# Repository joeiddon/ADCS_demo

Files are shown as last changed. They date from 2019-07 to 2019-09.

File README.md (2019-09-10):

ADCS Demo
=========

#### An Attitude Determination and Control System (ADCS) demo.

Created for [Open Cosmos](https://www.open-cosmos.com/), this project uses off-the-shelf components to demonstrate the principle of operation of an ADCS.

See videos and pictures of the development process and a working protoype in [this Google Photos Album](https://photos.app.goo.gl/isr3sSZi2DETxmJA6).

---

### What is an ADCS?

This system is an essential component of most spacecraft. It is the general term for the hardware and software which keeps a satellite orientated in space.

Although the objective of an ADCS is common amongst all systems, the way this is achieved varies. The many different variations and their characteristics are summarised in [this NASA paper](https://ntrs.nasa.gov/archive/nasa/casi.ntrs.nasa.gov/20110007876.pdf).

### Reaction wheel as the actuator

A wide variey of actuator types can be used in an ADCS. For example: magnetic torquers, thrusters and reaction wheels. This demo uses a reaction wheel.

A reaction wheel works by spinning a wheel up to a high angular velocity, then applying a torque to change this velocity. Due to Newton's Third Law, the body must experience an equal and opposite torque to the wheel - accelerating it in the opposite direction. Alternatively, this could be thought of in terms of the [law of conservation of angular momentum](http://www.feynmanlectures.caltech.edu/I_18.html) if we assume no external torque on the system as a whole.

Through a PID feedback loop, this mechanism can precisely control the orientation of a spacecraft.

The sensor used as an input to this PID loop varies for real applications (e.g. Sun sensor, Earth sensor, Star Tracker, Magnetometer etc.). This demo was designed to track the position of a torch, so two light sensors are used; their difference in readings providing an error value to work with.

### Demo hardware specifics

Three reaction wheels would be required to orient in all three axis. For simplicity of design, this demo focusses on controlling the attitude in a singular axis. In order to do this, the demo is freely suspended by a piece of thread which isolates the vertical axis.

The demonstration consists of the following components:

Part | Component Type Used
--- | ---
Processor | Arduino Nano
Motor | Brushless DC from Hard Drive
Frame | 3D Printed; Designed in OpenScad
Power | Two 1S Lipos in Series (7.4V)
Light Sensors | LDRs

### Prototype

To verify that the above set of components would be appropriate, a prototype was built first ([video](https://photos.app.goo.gl/x1hWNtvbokYaZJKe7)). This used a breadboard to host the MOSFET power distribution, and a bench power supply instead of lipo batteries. It suceeded in proving that, amongst other things, the motor would be adequate.

### Pictures

Below are some pictures of the design process. For more images, see the `images` directory.

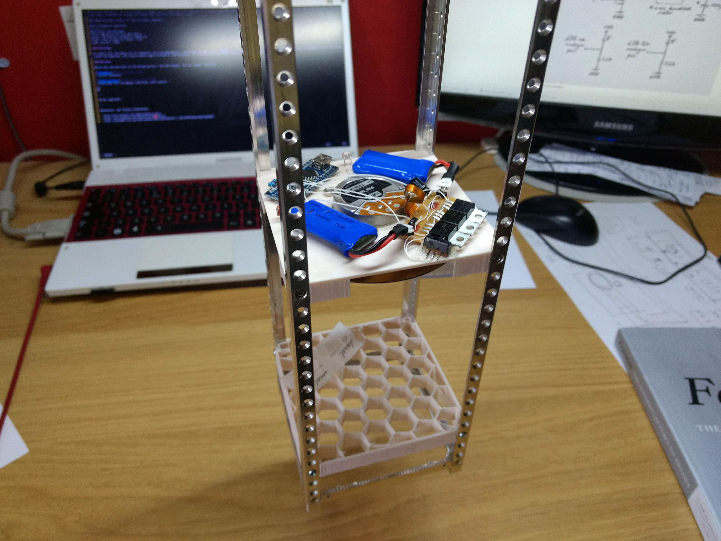
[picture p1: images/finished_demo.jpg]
Finished Demo

*Finished Demo*

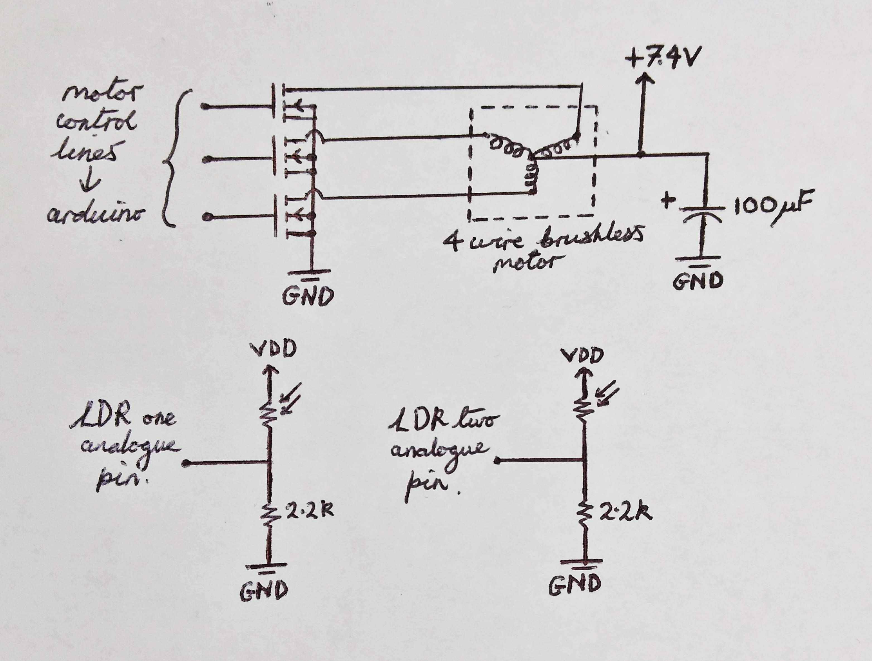
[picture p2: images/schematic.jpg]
Schematic

*Circuit schematic* ([better diagram](https://xkcd.com/730/))

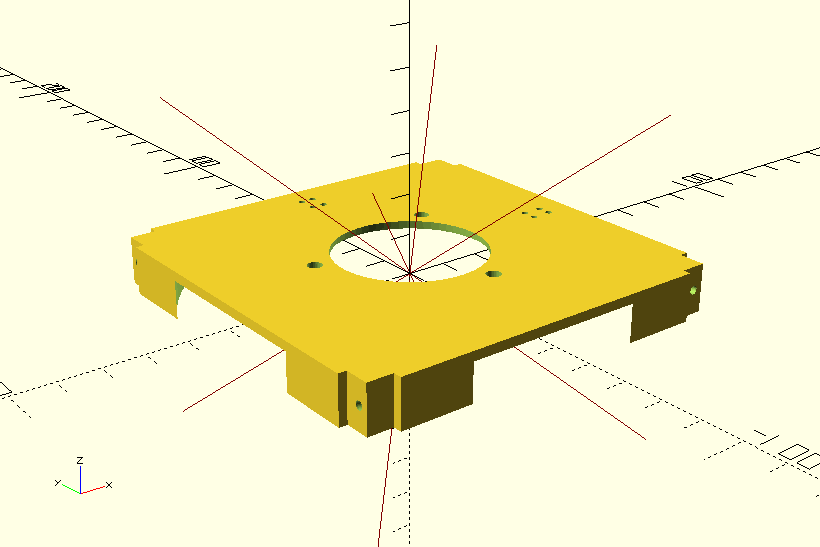
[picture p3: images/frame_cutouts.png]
Frame Cutouts

*Frame that fits the BeeKit interface; with cutouts.*

---

#### References, and further information:

- http://www.ece3sat.com/cubesatmodules/adcs/
- https://en.wikipedia.org/wiki/Attitude_control
- http://citeseerx.ist.psu.edu/viewdoc/download?doi=10.1.1.823.8473&rep=rep1&type=pdf

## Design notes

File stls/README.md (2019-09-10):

This folder contains the `.stl` 3D model files that are ready to be sent to a 3D printer to be sliced and printed.

For descriptions of the designs, see the README in the sibling `/scads` directory.

To view any particular design just click on it and GitHub will render it here in the browser for you.

You can then right click on the `Raw` button and select "Save link as..." to download it if you do not want to clone this whole repository.

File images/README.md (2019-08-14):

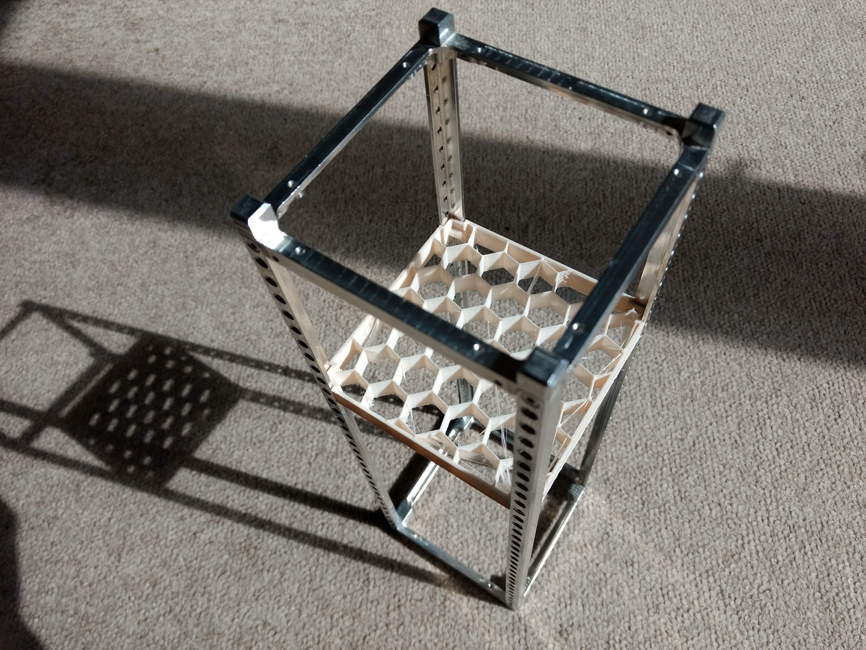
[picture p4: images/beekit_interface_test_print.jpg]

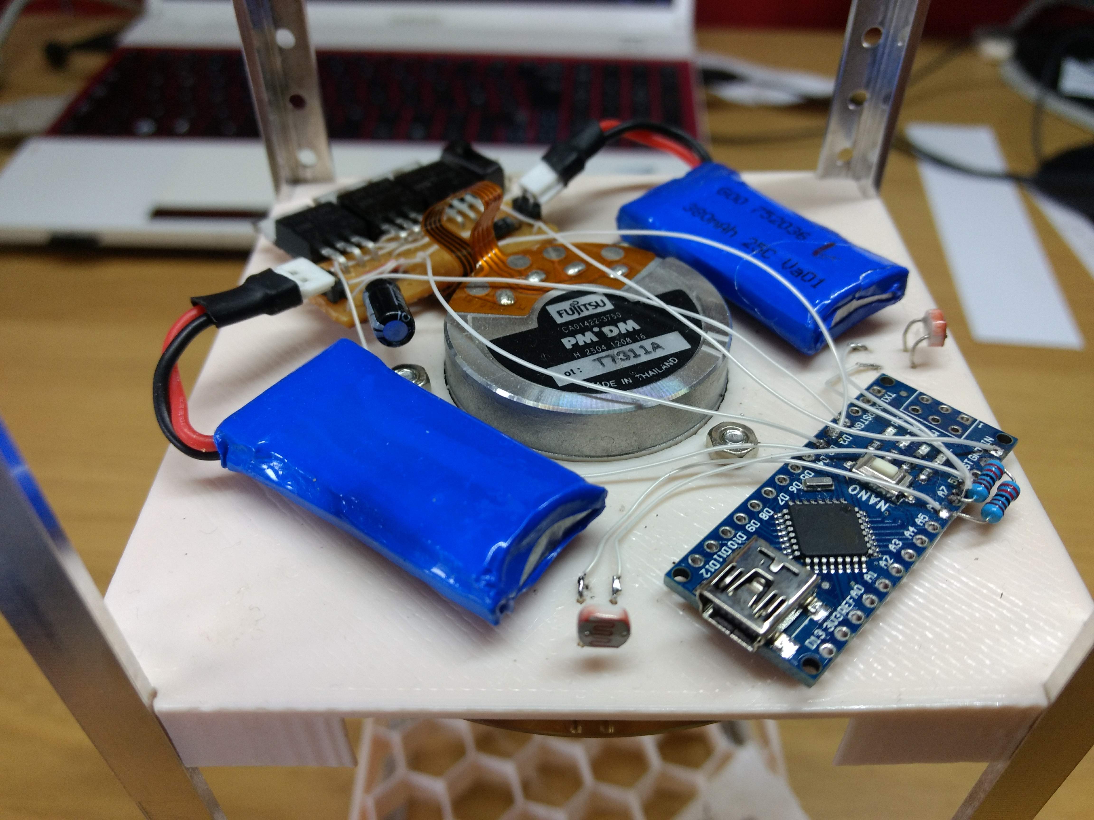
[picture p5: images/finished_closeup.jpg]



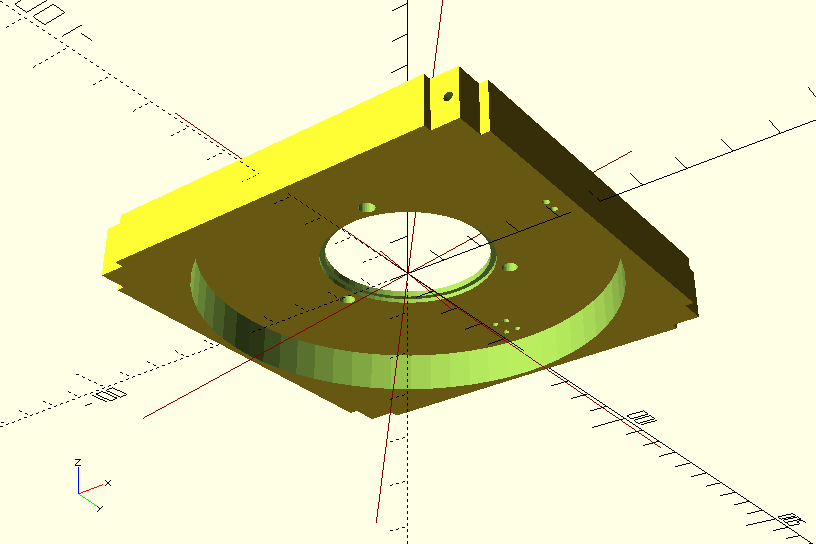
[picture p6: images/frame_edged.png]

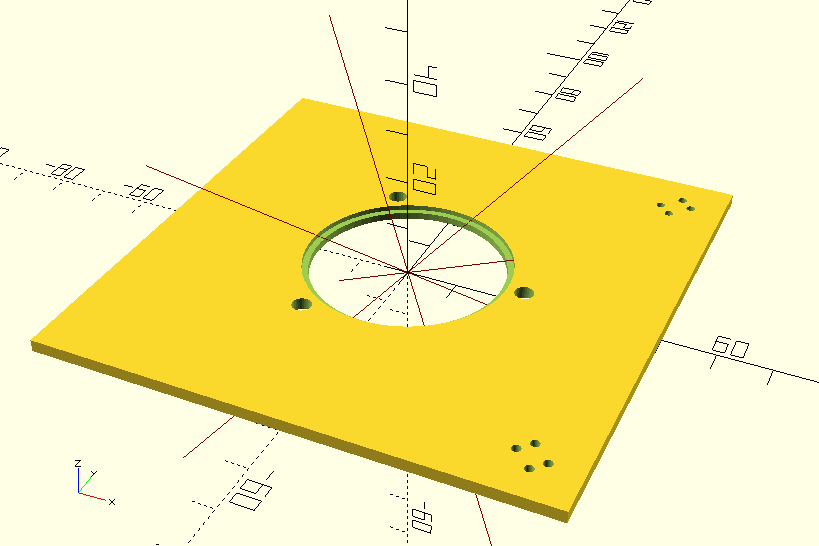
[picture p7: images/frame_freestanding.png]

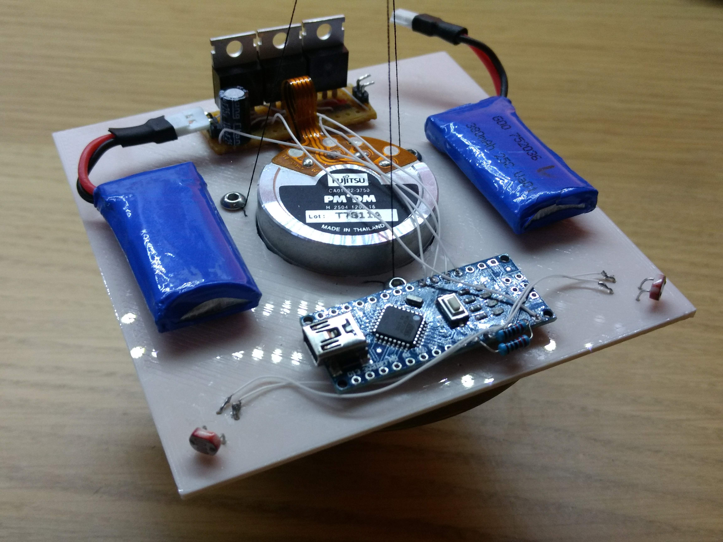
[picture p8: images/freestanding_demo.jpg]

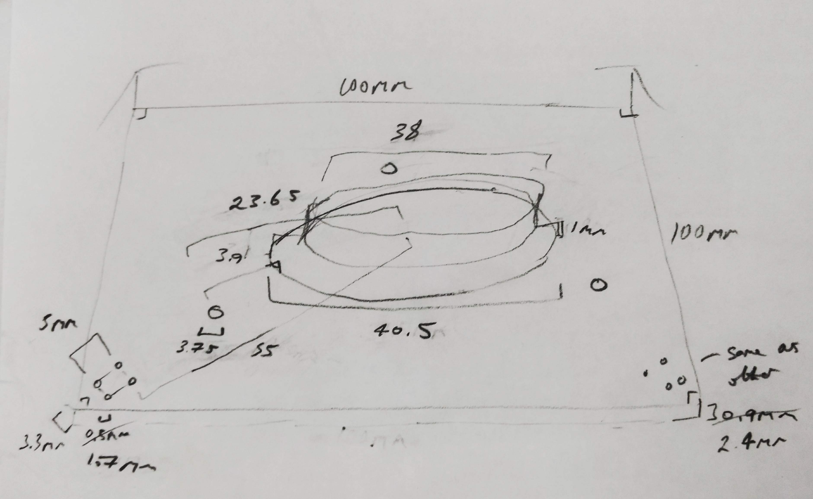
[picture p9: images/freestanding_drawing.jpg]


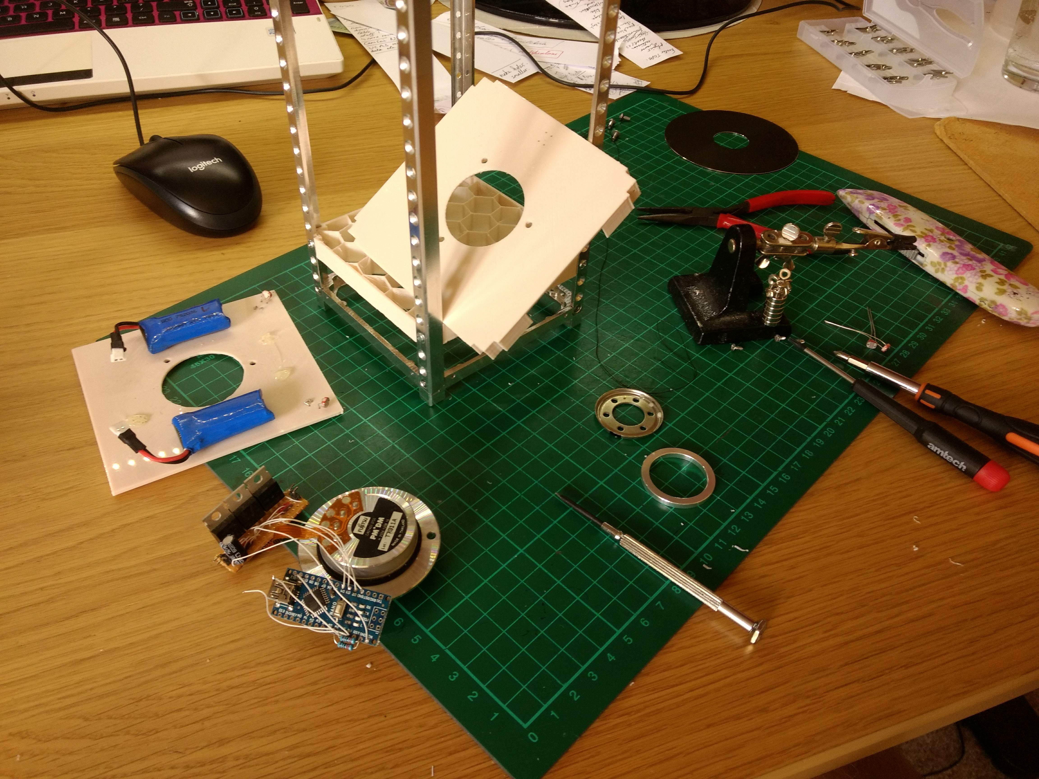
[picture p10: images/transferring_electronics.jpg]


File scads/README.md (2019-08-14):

These are the OpenSCAD source files (code) that are used to generate diffrent 3D frame designs for the demo.

In the `stls` folder in the parent directory, you can find the `.stl` 3D model files exported from OpenSCAD using this source.

All files prefixed with `frame_` contain different designs for the demo.

The first design, `frame_freestanding.scad`, can be suspended as a standalone demo; hence it does not fit the BeeKit.

The later designs, which fit the BeeKit, are `frame_cutouts.scad` and `frame_edged.scad`. These are literally identical files, bar the `wheel_cutouts_diameter` variable. In the `frame_cutouts.scad` file this is set to be larger than `100mm` so that there are cutouts in the walls of the BeeKit module. Conersely, the `frame_edged.scad` has a value less than `100mm` so that the BeeKit interface has full walls all the way around - so it is "edged". If this is not clear, see the renders of their corresponding `.stl` files here in GitHub.

I only ever 3D printed and tested the `frame_cutouts.scad` design since I felt it served better as a demonstration. I leave the `frame_edged.scad` design here in case someone wishes to modify this in the future.

Finally, the `beekit_interface.scad` file contains a single module: `beekit_interface(layers)`. This returns a solid structure that spans "layers" many mounting holes in the BeeKit frame. Both `frame_edged.scad` and `frame_cutouts.scad` use this. Again, this code may come in useful for a future developer working in OpenSCAD.

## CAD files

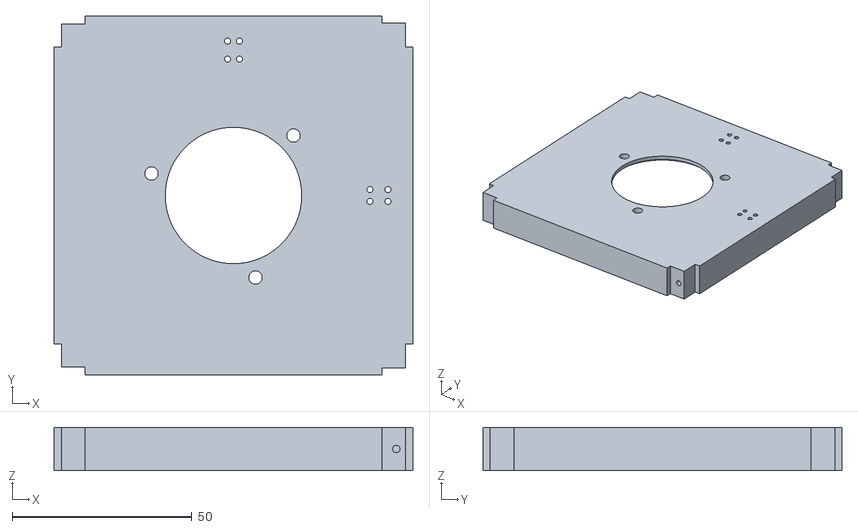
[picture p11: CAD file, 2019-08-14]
stls/frame_edged.stl
100.0 x 100.0 x 12.0

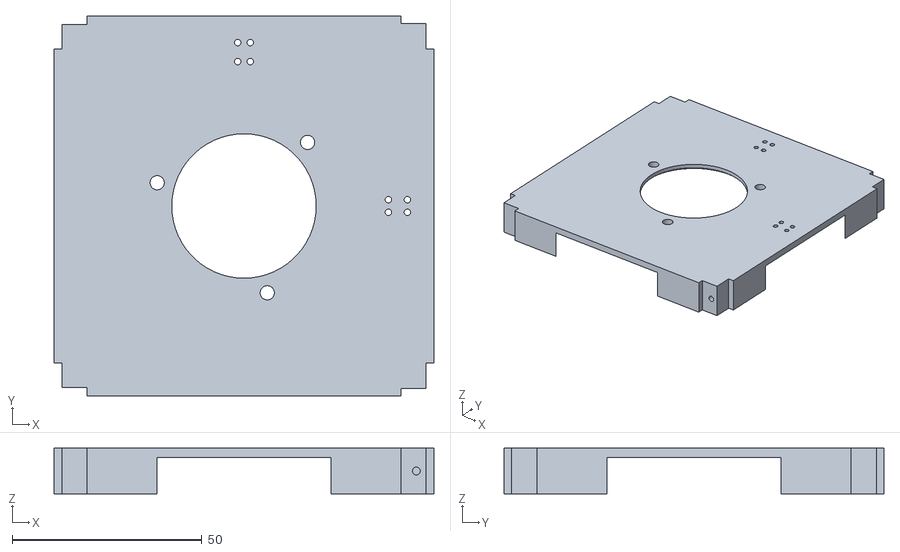
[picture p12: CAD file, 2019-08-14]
stls/frame_cutouts.stl
100.0 x 100.0 x 12.0

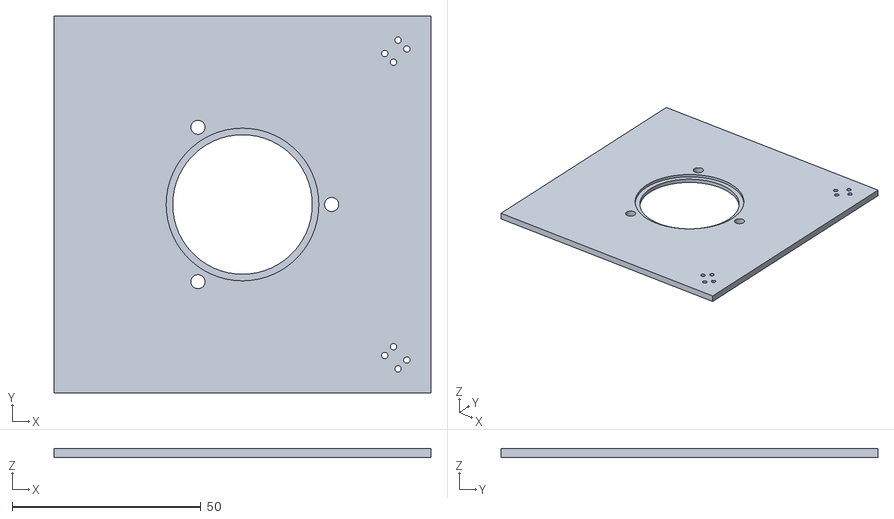
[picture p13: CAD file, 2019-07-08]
stls/frame_freestanding.stl
100.0 x 100.0 x 2.40

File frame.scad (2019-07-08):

$fn = 30;
length = 100;
thickness = 2.4;
motor_ring_thickness = 1;
motor_ring_diameter = 40.5;
motor_diameter = 38;
screw_hole_diameter = 3.75;
screw_hole_dist = 23.65;
ldr_hole_diameter = 1.7;
ldr_hole_width = 3.3;
ldr_hole_length = 5;
ldr_hole_dist = 55;

difference(){
    translate([0,0,thickness/2])
    cube([length,length,thickness],center=true);
    cylinder(d=motor_diameter,h=thickness,$fn=60);
    translate([0,0,thickness-motor_ring_thickness])
    cylinder(d=motor_ring_diameter,h=motor_ring_thickness,$fn=60);
    for (angle = [0,120,240]){
        rotate(angle)
        translate([screw_hole_dist, 0, 0])
        cylinder(d=screw_hole_diameter,h=thickness);
    }
    for (angle = [-45, 45]){
        rotate(angle)
        translate([ldr_hole_dist, 0, 0])
        ldr_holes();
    }
}

module ldr_holes(){
    translate([0,-ldr_hole_width/2,0])
    cylinder(d=ldr_hole_diameter,h=thickness);
    translate([0, ldr_hole_width/2,0])
    cylinder(d=ldr_hole_diameter,h=thickness);
    translate([ldr_hole_length,-ldr_hole_width/2,0])
    cylinder(d=ldr_hole_diameter,h=thickness);
    translate([ldr_hole_length, ldr_hole_width/2,0])
    cylinder(d=ldr_hole_diameter,h=thickness);
}

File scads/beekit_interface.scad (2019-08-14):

/*
Design by Joe Iddon.
*/

$fn = 30;

module beekit_interface(layers){
    //using dimensions in https://open-cosmos.com/beekit-usermanual
    //there is a dimension missing from that schematic though:
    //the width of every side with cutouts is 82.6 - this was confirmed
    //from an autodesk 360 model
    //x-axis points in same direciton as two of the fasteners
    //layers determines the height of this mechanical interface
    //module - e.g. a value of `2` means a height of (2*12+12)mm
    //so would have a potential of 16 holes to be screwed in to the
    //beekit frame
    width = 100; //square, so length = width
    cutout_width = 82.6; //width of all the "flat" sides (after cutouts)
    //meaning of all indent measurements seen from schematic
    x_indent = 95.8;
    y_indent_close = 95.6;
    y_indent_far = 96;
    hole_sep = 12; //vertical separation between screw holes
    buffer_height = 6; // (12 / 2) - so doesn't end on a screw hole
    hole_diameter = 2.1; //needs experimentation if 3d printing
    hole_dist = 2.55; //distance of screw holes from nearest edges
    hole_depth = 7; //random choice, schematic defined must be > 5
    
    height = (layers-1)*hole_sep+buffer_height*2;
    union(){
        cube([width,cutout_width,height], center=true);
        cube([cutout_width,width,height], center=true);
        translate([-x_indent/4,0,0])
        difference(){ //hole block facing the same way ("close")
            cube([x_indent/2,y_indent_close,height], center=true);
            for (hole = [0:layers-1])
            translate ([0,0,-height/2+buffer_height+hole*hole_sep]){
                translate([-x_indent/4,y_indent_close/2-hole_dist,0])
                rotate([0,90,0]) cylinder(d=hole_diameter,h=hole_depth);
                translate([-x_indent/4,-(y_indent_close/2-hole_dist),0])
                rotate([0,90,0]) cylinder(d=hole_diameter,h=hole_depth);
            }
        }
        translate([x_indent/4,0,0])
        difference(){ //hole block facing outwars ("far")
            cube([x_indent/2,y_indent_far,height], center=true);
            for (hole = [0:layers-1])
            translate([0,0,-height/2+buffer_height+hole*hole_sep]){
                translate([x_indent/4-hole_dist,y_indent_far/2,0])
                rotate([90,0,0]) cylinder(d=hole_diameter,h=hole_depth);
                translate([x_indent/4-hole_dist,-y_indent_far/2,0])
                rotate([-90,0,0]) cylinder(d=hole_diameter,h=hole_depth);
            }
        }
    }
}

beekit_interface(2);

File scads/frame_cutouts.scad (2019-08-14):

/*
Design by Joe Iddon.
*/


/*** PRINT DESIGN UPSIDE DOWN TO AVOID USING SUPPORTS ***/

use <beekit_interface.scad> //need the `beekit_interface(layers)` function

$fn = 30;

//parameters for ADCS system plate (so motor mounting and LDRs etc)
width = 100; //square, so length = width
thickness = 2.4; //thickness of plate
motor_ring_thickness = 1; //thickness of larger motor cutout ring
motor_ring_diameter = 40.5; //larger motor cutout ring diameter
motor_diameter = 38; //diameter of smaller motor cutout ring
screw_hole_diameter = 3.75; //diameter of holes for motor mounting
screw_hole_dist = 23.65; //distance of motor holes from center
ldr_hole_diameter = 1.7; //diameter of holes for LDR leads
ldr_hole_width = 3.3; //shorter distance between LDR lead holes
ldr_hole_length = 5; //longer distance between LDR lead holes
ldr_hole_dist = 38; //distance of close LDR holes from center

//parameters for connection of ADCS system plate with beekit interface
wheel_cutout_diameter = 110; //diameter of cutout for momentum wheel (HDD disk)
total_height = 12; //total height of the frame (2*buffer_height in beekit_interface)

intersection(){
    beekit_interface(1);
    difference(){
        union(){
            translate([0,0,total_height/2-thickness])
            ADCS_plate();
            translate([-width/2,-width/2,-total_height/2])
            cube([width,width,total_height-thickness]);
        }
        translate([0,0,-total_height/2])
        cylinder(d=wheel_cutout_diameter,h=total_height-thickness,$fn=60);
    }
}

module ADCS_plate(){
    difference(){
        translate([0,0,thickness/2])
        cube([width,width,thickness],center=true);
        cylinder(d=motor_diameter,h=thickness,$fn=60);
        //translate([0,0,thickness-motor_ring_thickness])
        cylinder(d=motor_ring_diameter,h=motor_ring_thickness,$fn=60);
        for (angle = [0,120,240]){
            rotate(angle+45)
            translate([screw_hole_dist, 0, 0])
            cylinder(d=screw_hole_diameter,h=thickness);
        }
        for (angle = [0,90]){
            rotate(angle)
            translate([ldr_hole_dist, 0, 0])
            ldr_holes();
        }
    }
}

module ldr_holes(){
    translate([0,-ldr_hole_width/2,0])
    cylinder(d=ldr_hole_diameter,h=thickness);
    translate([0, ldr_hole_width/2,0])
    cylinder(d=ldr_hole_diameter,h=thickness);
    translate([ldr_hole_length,-ldr_hole_width/2,0])
    cylinder(d=ldr_hole_diameter,h=thickness);
    translate([ldr_hole_length, ldr_hole_width/2,0])
    cylinder(d=ldr_hole_diameter,h=thickness);
}

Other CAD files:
scads/frame_edged.scad
scads/frame_freestanding.scad

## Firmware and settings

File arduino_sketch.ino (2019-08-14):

/*
 *  Code finalised in July 2019.
 */


/* 
 *  The Brushless DC HDD motor is three phased meaning it has
 *  three control lines that need to be pulsed correctly
 *  Pulses to the three motor phases overlap as follows.
 * 
 *  stage  0      1      2   |   0      1      2      ...
 *        __________            __________
 *  p1 __|          |__________|          |_________  ...
 *               __________            __________
 *  p2 _________|          |__________|          |___ ...
 *     ______            __________            _____
 *  p3       |__________|          |__________|       ...
 * 
 *  Notice how the pattern repeats after three "stages".
 * 
 *  BLDC motor takes 12 steps (4 phase cycles) to complete a full revolution.
 */

//TODO:
// get rid of floats
// slower speed

//digital pin nums of the three motor pins: p1, p2, p3
#define P1_PIN 2
#define P2_PIN 3
#define P3_PIN 4

//analogue pin nums for the two LDRs
#define LDR1_PIN 6
#define LDR2_PIN 7

//how many time is a pin 
#define STEPS_PER_REV 12

//some little macros
#define CLAMP(X) ((X) > 1 ? 1 : X)
#define ABS(X) ((X) < 0 ? -X : X)
//gives pulse interval time from rpm speed
#define PULSE_US_FROM_RPM(R) ((1000000 * 60) / ((R) * STEPS_PER_REV)) //[1000us for 5000rpm]
//gives accel interval from accel rate
#define INTERVAL_US_FROM_RATE(R) (1000000 / ABS((R)))
//gives pulse end time form start time
#define P_END_US(T) ((T) + (1 + 2 * overlap) * pulse_length_us)

#define PID_EVAL_US 1000 //time between re-evaluating PIDs

/////////////////////////////////////////////////////////////////////
/*** TUNING ***/
/* 
 *  In theory, these are the only constants that need changing.
 */

//PID tuning
#define KP 2
#define KD 0

#define INITIAL_ACCEL 270 //unit: rpm/sec
#define STARTUP_RPM 40
#define MAX_RPM 5000 //really 5400 but that is pushing it!

/*
 *  The overlap of the motor phases is designed to be proportional
 *  to the current rpm... when at slowest speed, the amount of
 *  overlap as a proportion is MAX_OVERLAP and max speed, MIN_OVERLAP.
 *  This is because more overlap is required at slower speeds. But a
 *  higher overlap draws more current, so the motor heats up more.
 */

#define MAX_OVERLAP 0.15  //overlap when current_rpm = 0
#define MIN_OVERLAP -0.2 //overlap when current_rpm = MAX_RPM

//////////////////////////////////////////////////////////////////////

//fraction of pulse_length that overlaps into next phase's pulse
float overlap = MAX_OVERLAP;

uint16_t current_rpm = STARTUP_RPM;
int16_t acceleration = INITIAL_ACCEL;

uint8_t has_done_initial_speed_up = 0;

//see the comment at start of loop() for reason for these
//the `us` suffix indicates a time in microseconds (10^{-6} seconds)
uint32_t last_pulse_us;
uint32_t last_accel_us;
uint32_t last_pid_us;
uint32_t loop_us;

//length of a pulse; ignoring the overlap - so really length of a stage
uint32_t pulse_length_us;
uint8_t stage = 0; //refer to ASCII for meaning; stage in {0,1,2}
//start times for each of the three phases
uint32_t p1_start_us, p2_start_us, p3_start_us;
//end times for each of the three phases
uint32_t p1_end_us, p2_end_us, p3_end_us;

//last error reading from the LDRs for derivative term of PID
int16_t last_error = 0;

//mainloop returns immediate if truthy (set in finish() function)
uint8_t done = 0;

//DEBUGGING
#define DEBUG 0
#define SAMPLE_INTERVAL_MS 10
#define MEM_SIZE 500
int16_t memory[MEM_SIZE];
uint16_t memory_ind = 0;
uint8_t has_splurged = 0;
uint32_t last_mem_us;

void setup() {
    //set all pulses as outputs
    pinMode(P1_PIN, OUTPUT);
    pinMode(P2_PIN, OUTPUT);
    pinMode(P3_PIN, OUTPUT);
    pinMode(13, OUTPUT); //on-board 'L' LED will light when demo is live
    last_pulse_us = last_accel_us = last_pid_us = last_mem_us = micros();
    p1_start_us = p2_start_us = p3_start_us = UINT32_MAX;
    if (DEBUG) Serial.begin(9600);
    pulse_length_us = PULSE_US_FROM_RPM(current_rpm);
    digitalWrite(13, LOW);
}

void loop() {
    /*
     *  The mainloop is design to never block for anything. It cycles
     *  as fast as possible - mainly relooping without changing anything.
     *  This is because it must coordinate different tasks at the same
     *  time: updating the timings for the three motor pins (and setting
     *  the digital pins to what they should be); updating the current RPM
     *  depending on what the current acceleration is; and updating the
     *  acceleration when it is time to via the PID system.
     *
     *  There is also an additional scope for printing some debugging info
     *  to Serial. This only runs when DEBUG is truthy.
     */
    if (done) return;
    loop_us = micros();
    if ((loop_us - last_pulse_us) >= pulse_length_us){
        last_pulse_us += pulse_length_us;
        switch (stage = (stage + 1) % 3){
            //in each case, we set the time to start the pulse for the next phase
            case 0:
                p2_start_us = last_pulse_us + (1 - overlap) * pulse_length_us; break;
            case 1:
                p3_start_us = last_pulse_us + (1 - overlap) * pulse_length_us; break;
            case 2:
                p1_start_us = last_pulse_us + (1 - overlap) * pulse_length_us; break;
        }
    }
    
    //Only set a pin high if it is after its "start time" and before the
    //end time which is calculated on-the-fly.
    digitalWrite(P1_PIN, (p1_start_us < loop_us) && (loop_us < P_END_US(p1_start_us)));
    digitalWrite(P2_PIN, (p2_start_us < loop_us) && (loop_us < P_END_US(p2_start_us)));
    digitalWrite(P3_PIN, (p3_start_us < loop_us) && (loop_us < P_END_US(p3_start_us)));
    
    if (acceleration && (loop_us - last_accel_us) >= INTERVAL_US_FROM_RATE(acceleration)){
        last_accel_us += INTERVAL_US_FROM_RATE(acceleration);
        if (has_done_initial_speed_up){
            current_rpm += acceleration > 0 ? 1 : -1;
            if (current_rpm > MAX_RPM) current_rpm = MAX_RPM;
            if (current_rpm == 0) finish(); //unsigned so no point in <= 0
            pulse_length_us = PULSE_US_FROM_RPM(current_rpm);
            overlap = MAX_OVERLAP - (MAX_OVERLAP - (MIN_OVERLAP)) * current_rpm / MAX_RPM;
        } else {
            if (current_rpm == MAX_RPM){
                has_done_initial_speed_up = 1;
                acceleration = 0;
                digitalWrite(13, HIGH);
                last_pid_us = last_mem_us = loop_us;
            } else {
                current_rpm += 1;
                pulse_length_us = PULSE_US_FROM_RPM(current_rpm);
                overlap = MAX_OVERLAP - (MAX_OVERLAP - (MIN_OVERLAP)) * current_rpm / MAX_RPM;
            }
        }
    }
    
    if (has_done_initial_speed_up && (loop_us - last_pid_us) >= PID_EVAL_US){
        last_pid_us += PID_EVAL_US;
        
        int16_t error = get_error();
        int16_t p = -KP * error;
        int16_t i = -120; //offset to counteract wind constant error - should really include a proper integral calc
        int16_t d =  KD * (last_error - error);
        acceleration = p + i + d;
        
        last_error = error;
    }

    //DEBUGGING
    if (DEBUG && !has_splurged && has_done_initial_speed_up && (loop_us - last_mem_us) >= SAMPLE_INTERVAL_MS * 1000){
        last_mem_us += SAMPLE_INTERVAL_MS * 1000;
        if (memory_ind + 3 >= MEM_SIZE){
            for (uint16_t i = 0; i < MEM_SIZE; i+=3){
                Serial.print(memory[i]);
                Serial.print(" ");
                Serial.print(memory[i+1]);
                Serial.print(" ");
                Serial.print(memory[i+2]);
                Serial.println();
            }
            finish();
        } else {
            memory[memory_ind++] = get_error();
            memory[memory_ind++] = acceleration;
            memory[memory_ind++] = 0;
        }
    }
}

void finish(){
    digitalWrite(P1_PIN, LOW);
    digitalWrite(P2_PIN, LOW);
    digitalWrite(P3_PIN, LOW);
    digitalWrite(13, LOW);
    done = 1;
}

int16_t get_error(){
    return analogRead(LDR1_PIN) - analogRead(LDR2_PIN);
}

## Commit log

2019-07-08 Initial Population.
    [frame.scad, frame.stl]
2019-08-14 Re-designed the frame to fit the BeeKit, so corresponding documentation here.
    [beekit_interface.scad, frame_cutouts.scad, frame_cutouts.stl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]
